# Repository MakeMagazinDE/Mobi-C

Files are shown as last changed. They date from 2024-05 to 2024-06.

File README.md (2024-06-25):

GitHub Logo

Maker Media GmbH

***

# Mobi-C

## Die mobile CNC-Fräse

**Dieser handliche X-Y-Positionierer für die Oberfräse ist schnell und einfach nachgebaut – dank fertig auf Länge bestellter Alu-Profile und Verbindungsteilen aus dem 3D-Drucker. Das ganze ist leicht zu transportieren, wird komplett mit Akkus betrieben und fräst auch in Werkstücke, die viel größer sind, als der Rahmen selbst.**

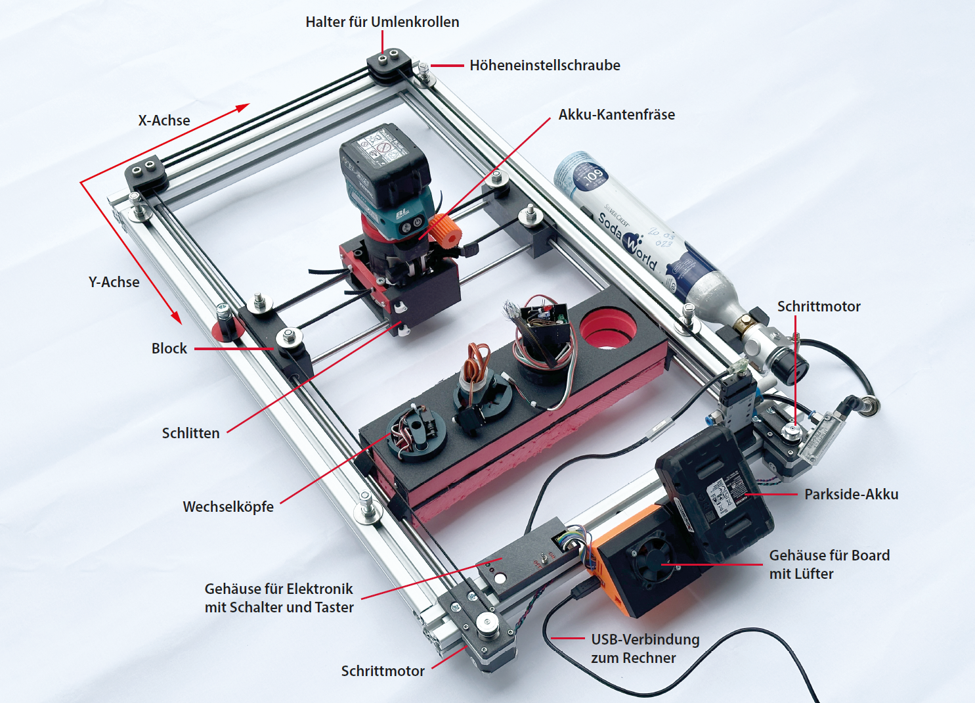
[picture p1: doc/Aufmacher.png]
Aufmacherbild aus dem Heft


Hier gibt es alles rund um den Nachbau der eigenen Mobi-C:

* Im Ordner _[cad](./cad/)_ liegt das 3D-Modell der Mobi-C als STEP-Datei und Projekt für Autodesk-Fusion 
* Im Ordner _[doc](./doc/)_ liegt unter anderem der [Schaltplan](./doc/schema.png)
* Im Ordner _[3d](./3d/)_ liegen die 3D-Druckvorlagen als STL-Dateien und gruppiert als 3mf, Details dazu weiter unten im Abschnitt **3D-Drucke**
* Im Ordner _[src](.src/)_ liegt das AutoHotkey-Skript fürs Einbauen der Pausen in den G-Code und im Zip-Archiv die EXE-Version davon

Der vollständige Artikel zum Projekt steht in der **[Make-Ausgabe 3/24 ab Seite 26](https://www.heise.de/select/make/2024/3/2401616284584453190)**. Einen ergänzenden Artikel mit weiteren Details zur Höhenverstellung, zur Frästiefen-Einstellung, zur Schleppmesser-Erweiterung und ein paar Erfahrungswerten gibt es **[online](https://heise.de/-9718002)**.

# Materialliste und Bezugsquellen
Vor einer Bestellung sind mit Hilfe der Tabelle im Heft und anhand der gewünschten Arbeitsbereichsgröße der eigenen Mobi-C die nötigen Profillängen **X** und **Y** sowie die Gleitstangenlängen **GX** und **GY** zu ermitteln.

* [2 Aluminiumprofile 40×40×**X** mm, Nut 8](https://www.dold-mechatronik.de/Aluminiumprofil-40x40L-I-Typ-Nut-8-leicht-176kg-m-Zuschnitt-50-6000mm)
* [2 Aluminiumprofile 40×40×**Y** mm, Nut 8, M8-Gewinde an den Stirnseiten anbringen lassen](https://www.dold-mechatronik.de/Aluminiumprofil-40x40L-I-Typ-Nut-8-leicht-176kg-m-Zuschnitt-50-6000mm)
* [2 Präzisionswellen 8×**GX**, geschliffen und gehärtet](https://www.dold-mechatronik.de/Praezisionswelle-8mm-h6-geschliffen-und-gehaertet-Material-CF53-mit-Bearbeitung)
* [2 Präzisionswellen 8×**GY**, geschliffen und gehärtet](https://www.dold-mechatronik.de/Praezisionswelle-8mm-h6-geschliffen-und-gehaertet-Material-CF53-mit-Bearbeitung)
* [Zahnriemen GT2, 6 mm, Länge laut Tabelle im Heft](https://www.dold-mechatronik.de/Zahnriemen-GT2-Breite-6mm-Meterware-Laenge-6-Meter)
* [5 Nutensteine mit Steg I-Typ 8 mit M8-Gewinde](https://www.dold-mechatronik.de/Nutenstein-mit-Steg-I-Typ-Nut-8-Gewindedurchmesser-M8)
* [7 Nutensteine mit Steg I-Typ 8 mit M6 Gewinde](https://www.dold-mechatronik.de/Nutenstein-mit-Steg-I-Typ-Nut-8-Gewindedurchmesser-M6)
* [4 Zylinderschrauben DIN 912 M8×40 (Innensechskant) für die Umlenkrollen am Rahmen](https://www.dold-mechatronik.de/DIN-912-Zylinderschraube-mit-Innensechskant-88-verzinkt-M8x40)
* [4 Zylinderschrauben DIN 912 M8×60 (Innensechskant) für die Umlenkrollen der X-Achse](https://www.dold-mechatronik.de/DIN-912-Zylinderschraube-mit-Innensechskant-88-verzinkt-M8x60)
* [4 DIN 7984 Zylinderschraube mit Innensechskant und niedrigem Kopf für die Rahmenmontage](https://www.dold-mechatronik.de/DIN-7984-Zylinderschraube-mit-Innensechskant-und-niedrigem-Kopf-88-verzinkt-M8x16)
* [4 Scheiben DIN9021 M8 - 8.4×32](https://www.dold-mechatronik.de/Scheibe-DIN9021-M8-84X32X2-A2)
* [4 Scheiben DIN125A-84 × M8](https://www.dold-mechatronik.de/Scheibe-DIN125A-M8x84-A2)
* [8 Kugellager 608ZZ (8×22×7)](https://www.dold-mechatronik.de/608ZZ-Bearings-8-x-22-x-7)
* [2 Z30-GT2-6 Riemenscheiben 5 mm Bohrung, 16 mm Sitz](https://www.bastelgarage.ch/z30-gt2-6-riemenscheibe-5mm-bohrung-16mm-sitz?search=z30-gt2)
* [8 Gleitlager LM8UU (8 mm Welle, 15×24 mm)](https://www.dold-mechatronik.de/Linearlager-8mm-LM8UU)
* 1 Meter Gewindestange M8 oder drei Schrauben M8, 100 mm lang mit Vollgewinde für die Höhenverstellung
* [4 Gewindeeinsätze M4](https://www.reichelt.com/ch/de/3d-druck-gewindeeinsaetze-m4x8-1-50-stueck-rx-m4x8-1-p332215.html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)
* 4 selbstsichernde Muttern M8
* 2 Stepper-Motoren (ST42sth38-1684A)
* [Arduino Uno USB](https://www.reichelt.com/ch/de/arduino-uno-rev-3-smd-variante-atmega328-usb-arduino-uno-p119045.html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)
* [CNC-Shield mit 4 Treibern A4988](https://www.reichelt.com/ch/de/arduino-shield-cnc-controllerboard-a4988-ard-shd-cnc-kit-p226375.html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)
* Lüfter 40×40×20 mm 12 bis 24 Volt
* 2 Schalter
* 1 Taster 
* 2 LEDs (eine rote, eine grüne)
* 2 Büroklammern
* [Parkside-Akku und Ladegerät](https://www.lidl.de/p/parkside-20-v-akku-2-ah-pap-20-b1-und-ladegeraet-2-4-a-plg-20-c1/p100368935)

# 3D-Drucke

 Als Material für alle 3D-Druck-Teile hat sich PLA bewährt, bei 0,2  Millimetern Schichtdicke. Als Infill reichen 15 %, außer bei den  Motorhaltern, die brauchen 80 %. Folgende Bilder zeigen, wie die Teile auf der Druckplatte angeordnet und orientiert werden sollten. Support ist nur an wenigen Stellen nötig: unter den Rundungen der Umlenkrollengehäuse  sowie beim Parkland-Akku-Adapter, auf den Screenshots.  

1. Hier alle Teile für den Rahmen, grün erkennt man den Support unter den Rundungen der Umlenkrollengehäuse:
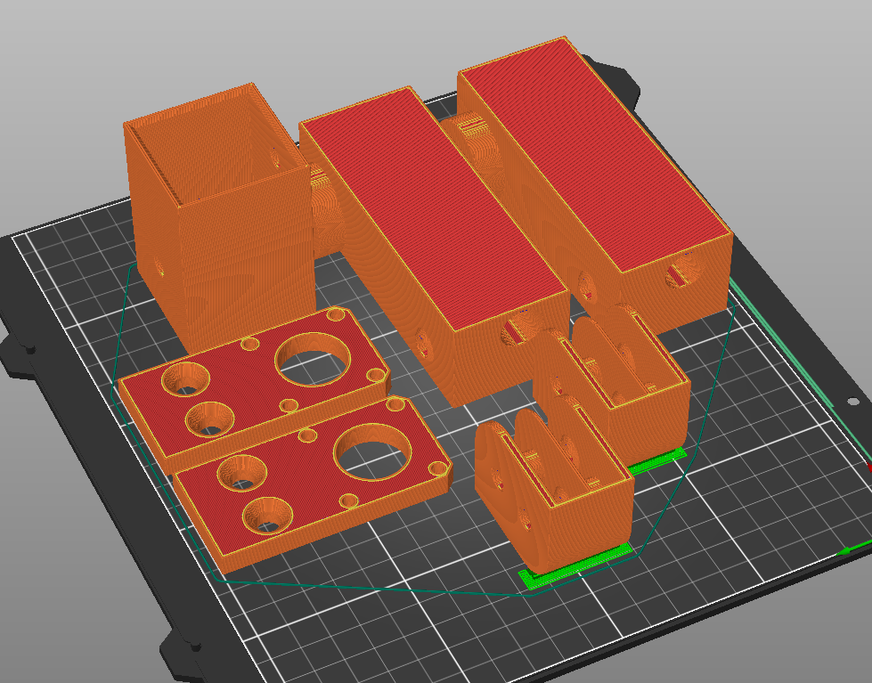
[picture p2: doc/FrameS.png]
Rahmen


2. Die Teile für den Schlitten werden nicht gestützt: 
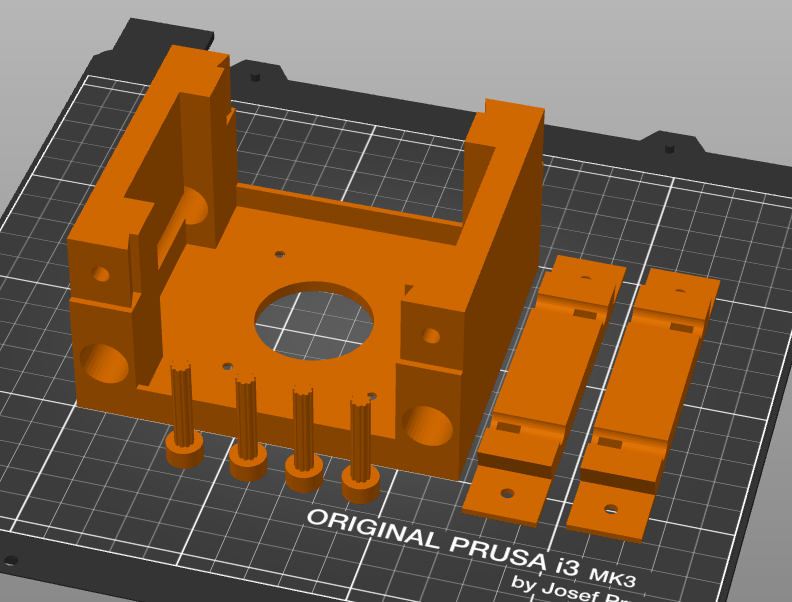
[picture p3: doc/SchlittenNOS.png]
Schlitten


3. Bei den Elektronikgehäusen muss der Adapter für den Parkside-Akku gestützt werden (vorne links):
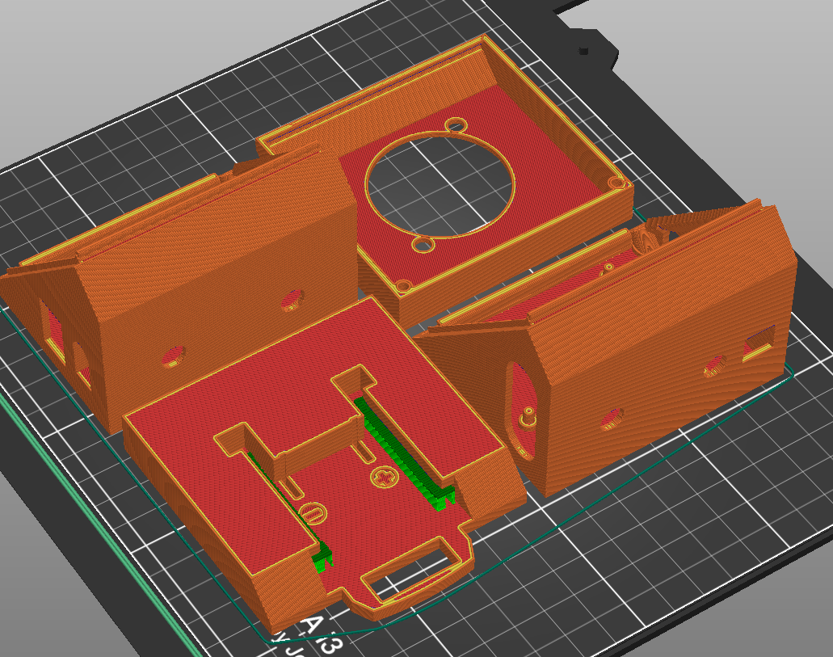
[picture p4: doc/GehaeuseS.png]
Elektronik


4. Das Schaltergehäuse braucht keine Stützen: 
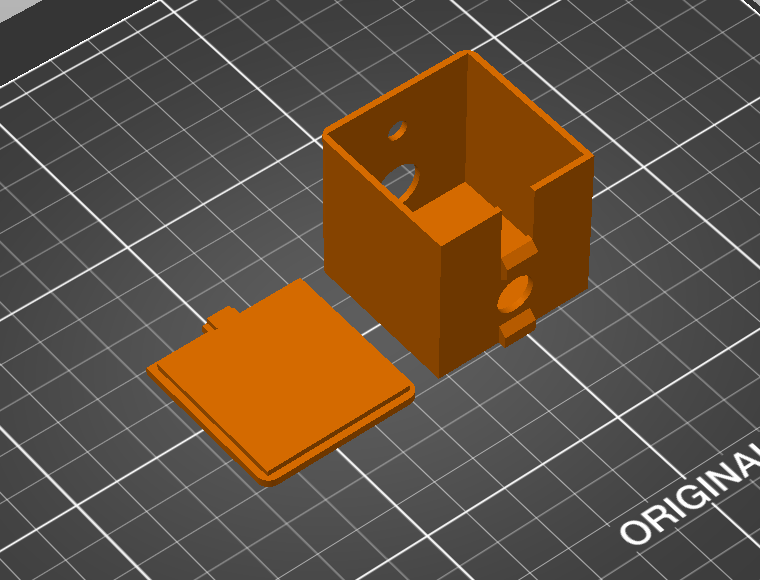
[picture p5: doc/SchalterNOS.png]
Schalter
   

5. Auch die Teile für die Makita müssen nicht gestützt werden:
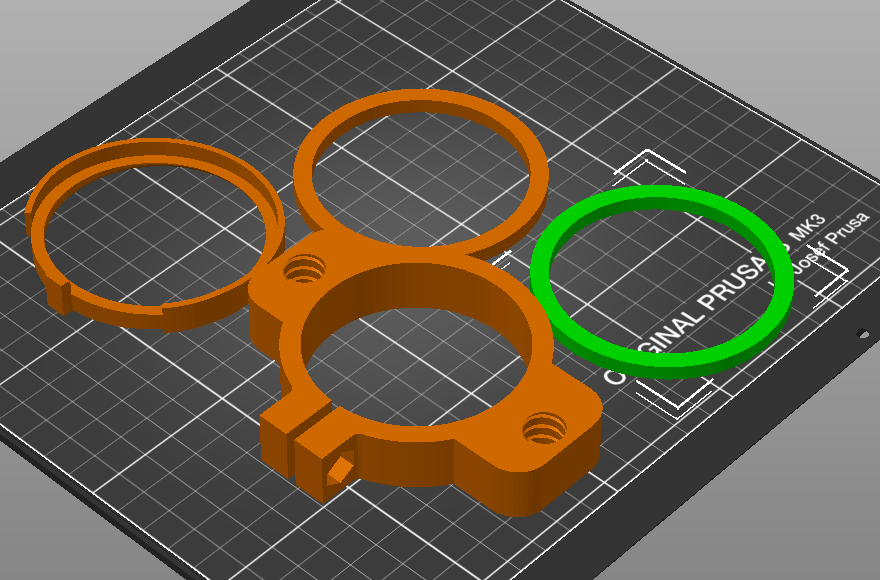
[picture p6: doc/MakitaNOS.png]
Makita
   

6. Die Ansicht für die Teile des Schleppmesseradapters sind hier der Deutlichkeit halber von schräg unten zu sehen: Grün bedeutet Support, die violette Fläche ist das erste Drucklayer:
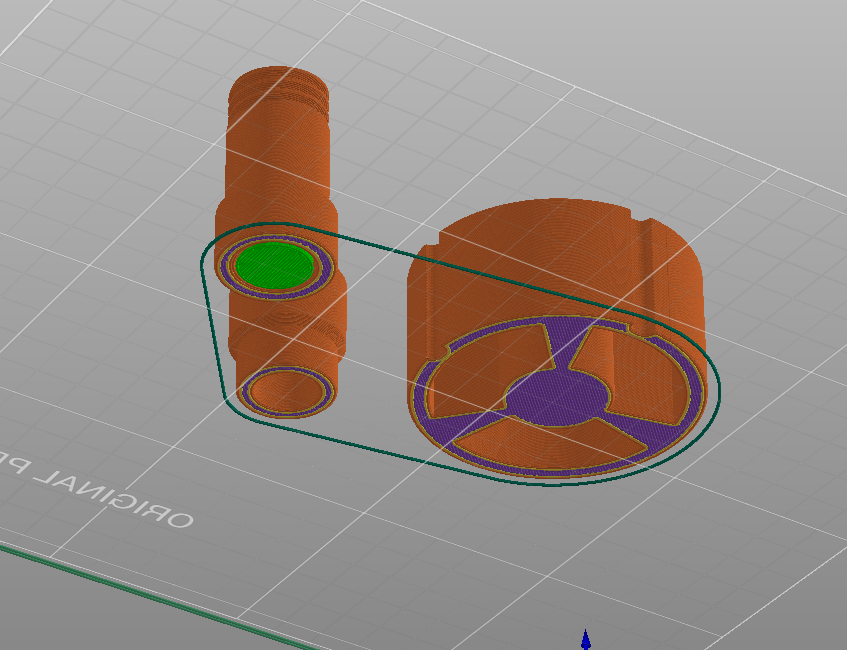
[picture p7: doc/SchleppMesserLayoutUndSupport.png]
Schleppmesser


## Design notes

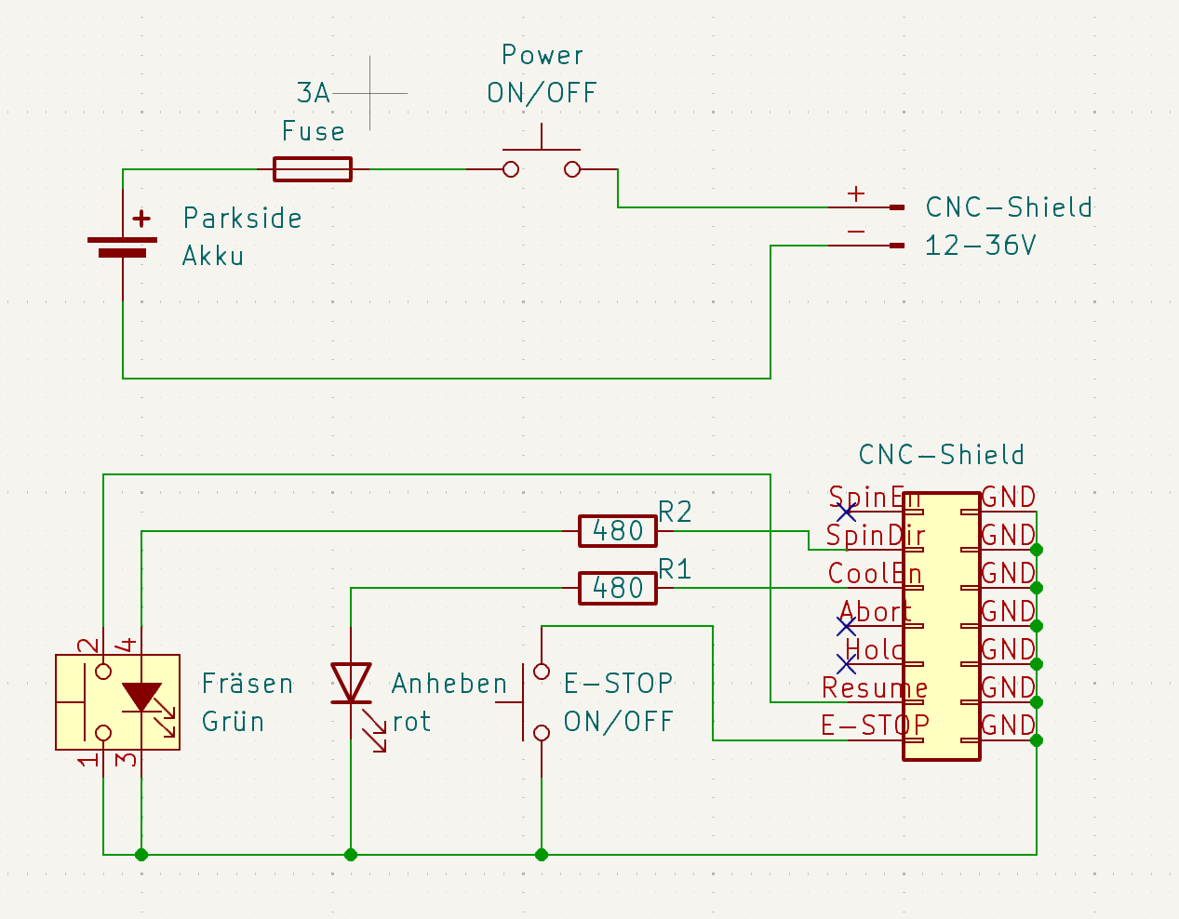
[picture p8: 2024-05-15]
doc/schema.png

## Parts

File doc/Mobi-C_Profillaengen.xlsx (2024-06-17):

Beschreibung | Anzahl | Länge [mm] | Max Länge [mm] | M8 Gewinde
Alu Profil 40x40 Richtung X-Achse | 2 | 470 | 480 | keine
Alu Profil 40x40 Richtung Y-Achse | 2 | 470 | 600 | beide Stirnseiten
Gleitstange X-Achse | 2 | 344 | 354
Gleitstange y-Achse | 2 | 510 | 640
Zahnriemen | 1 | 4260 | 4820
 | x-Richtung[mm] | y-Richtung[mm]
Arbeitsbereich | 216 | 352

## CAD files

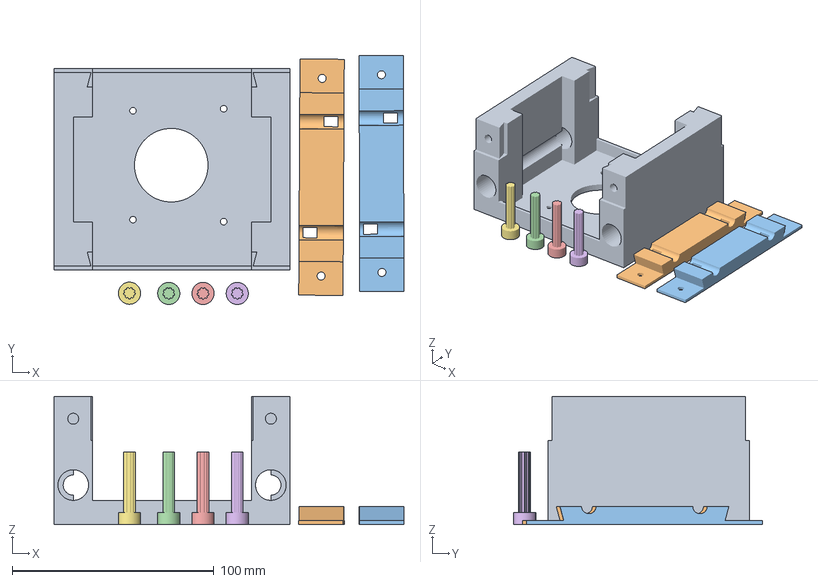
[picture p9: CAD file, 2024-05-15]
3d/Fraesschlitten/Fraesschlitten_complete_noSupports.3mf
173.6 x 123.5 x 63.6 mm
Fraesschlitten.stl
ZugRechtsLinks.stl
RiemenSpanner.stl

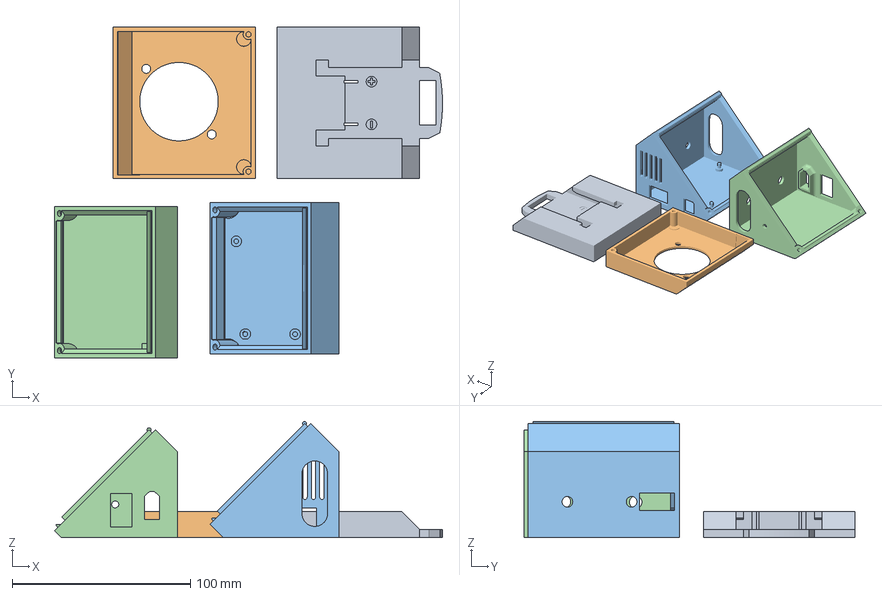
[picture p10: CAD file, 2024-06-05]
3d/ElectronikGehaeuse/ElectronicHousingComplete_Bambu.3mf
217.7 x 185.4 x 65.1 mm
lidl_parkside_20v_battery_adapter_front_85mm.stl
ElectronicHousing_front.stl
ElectronicHousing_rear.stl
lidl_parkside_20v_battery_adapter_rear_85mm.stl

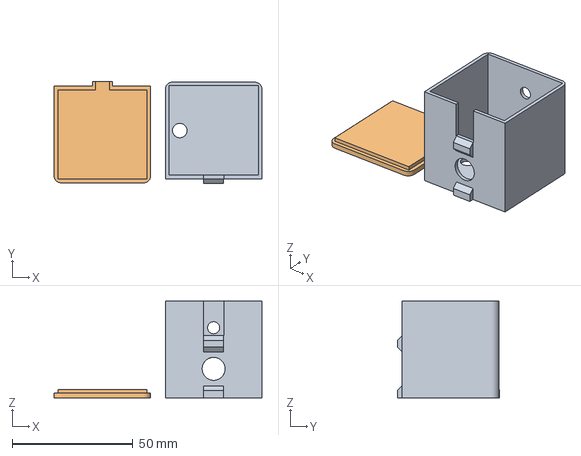
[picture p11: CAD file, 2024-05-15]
3d/ElectronikGehaeuse/SwitchLED_Housing_Complete.3mf
86.0 x 42.3 x 40.0 mm
SwitchCore.stl
SwitchCover.stl

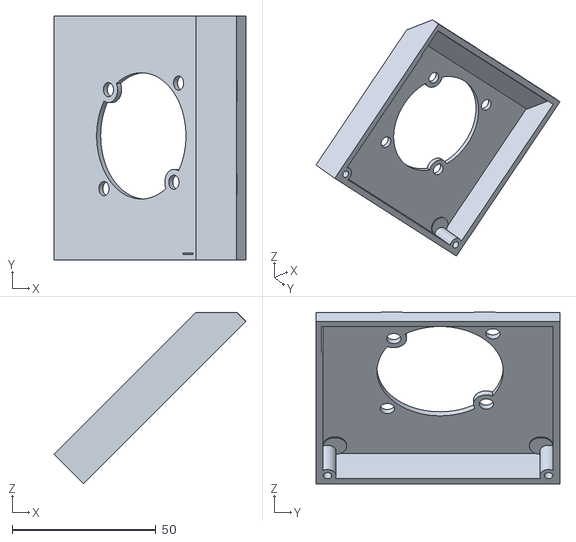
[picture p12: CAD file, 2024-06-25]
3d/ElectronikGehaeuse/ElectronicHousing_front.stl
66.9 x 85.0 x 59.8

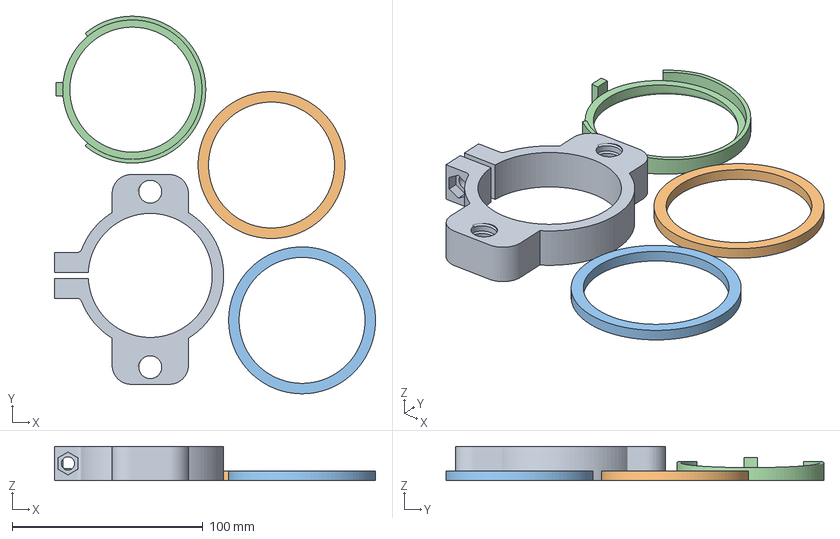
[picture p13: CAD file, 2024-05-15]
3d/MakitaZubehoer/MakitaZubehör_NoSupport.3mf
168.3 x 197.9 x 18.0 mm
StopBracket.stl
Distanzring_5mm.stl
FraesSchuh_Begradigung.stl

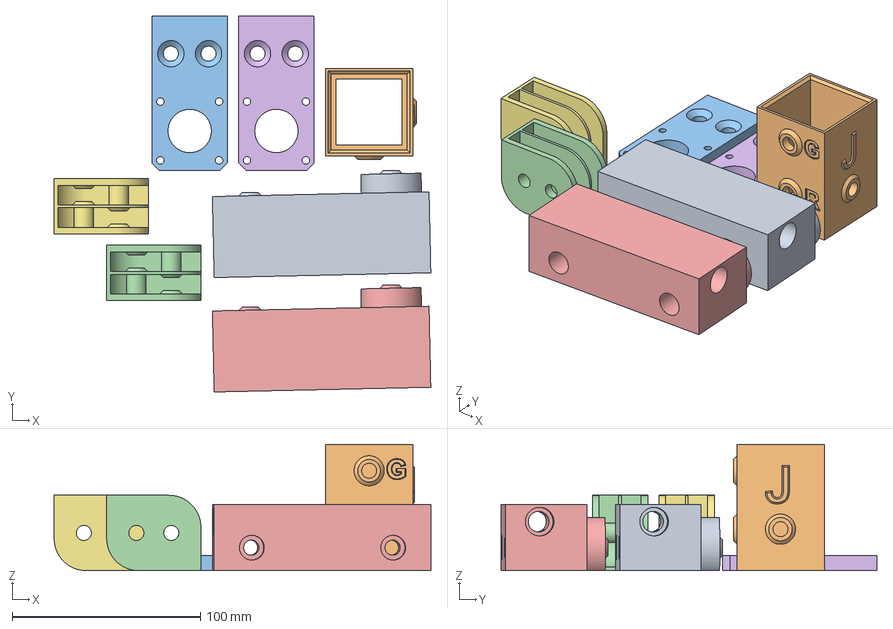
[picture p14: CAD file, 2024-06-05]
3d/Rahmen/Rahmen_LayoutAndSupport_Bambu0p6.3mf
199.9 x 199.5 x 67.0 mm
BlockXachse.stl x 2
BohrSchablone.stl
Motorhalter.stl x 2
UmlenkrollenGehaeuse.stl x 2

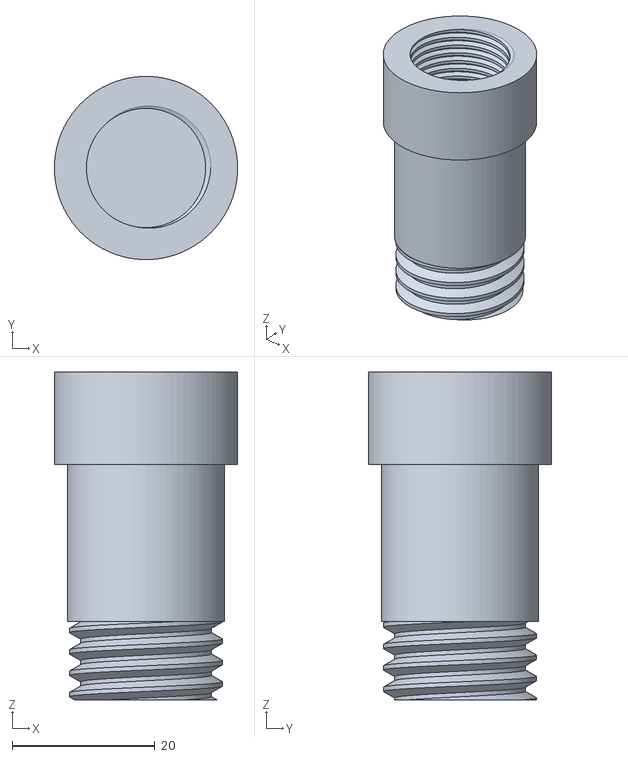
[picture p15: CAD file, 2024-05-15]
3d/Schleppmesser/HalterCore.stl
25.7 x 25.7 x 46.0

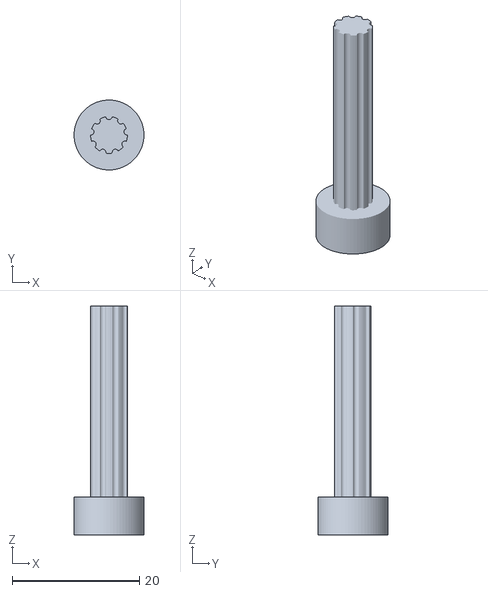
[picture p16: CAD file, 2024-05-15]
3d/Fraesschlitten/RiemenSpanner.stl
11.0 x 11.0 x 36.0

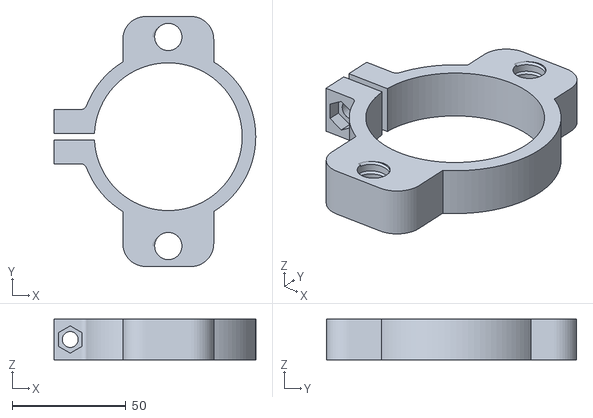
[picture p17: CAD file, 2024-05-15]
3d/MakitaZubehoer/StopBracket.stl
88.7 x 110.0 x 18.0

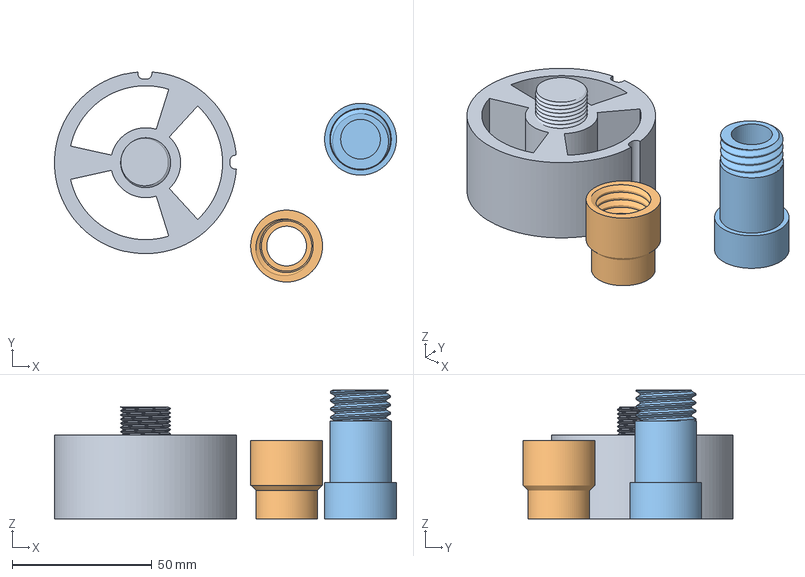
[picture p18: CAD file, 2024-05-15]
3d/Schleppmesser/SchleppMesserAdapter.3mf
122.3 x 75.1 x 46.0 mm
SchleppMesserAdapter.stl
HalterKappe.stl
HalterCore.stl

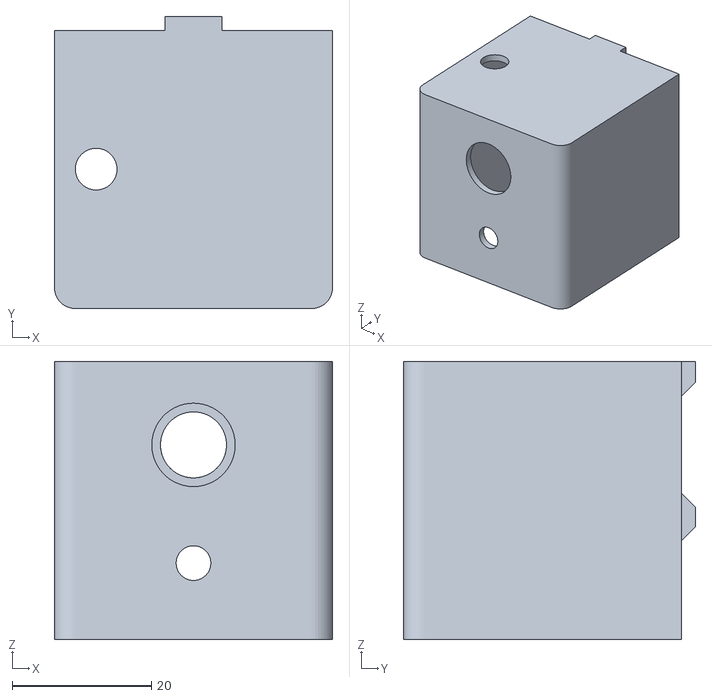
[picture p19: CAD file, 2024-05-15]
3d/ElectronikGehaeuse/SwitchCore.stl
40.0 x 42.0 x 40.0

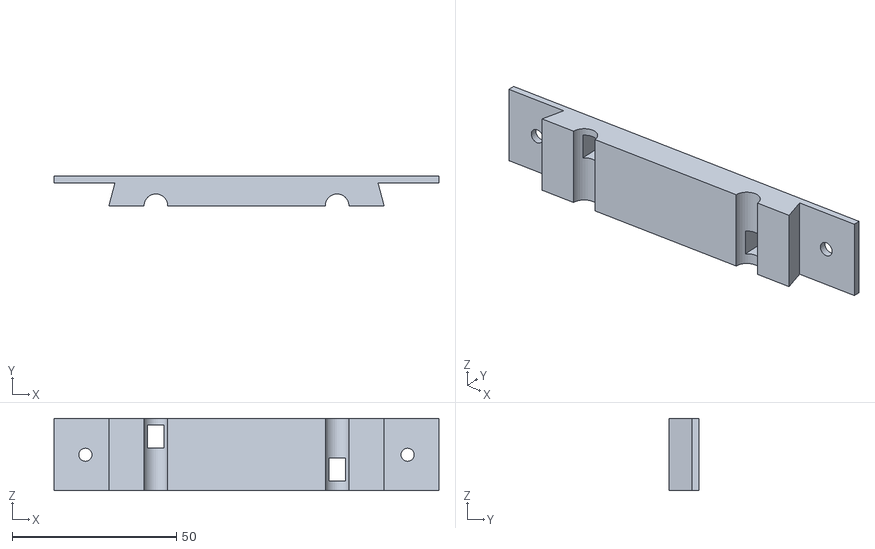
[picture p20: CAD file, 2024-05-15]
3d/Fraesschlitten/ZugRechtsLinks.stl
117.1 x 9.00 x 22.0

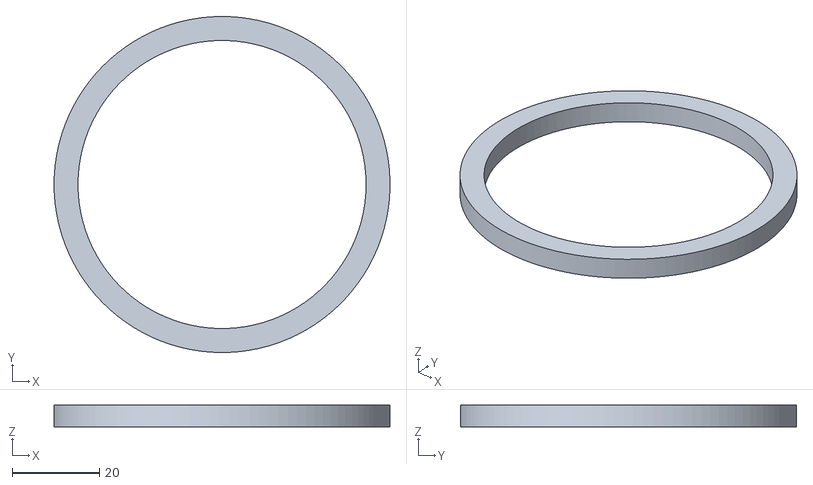
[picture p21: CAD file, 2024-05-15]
3d/MakitaZubehoer/Distanzring_5mm.stl
77.0 x 77.0 x 5.00

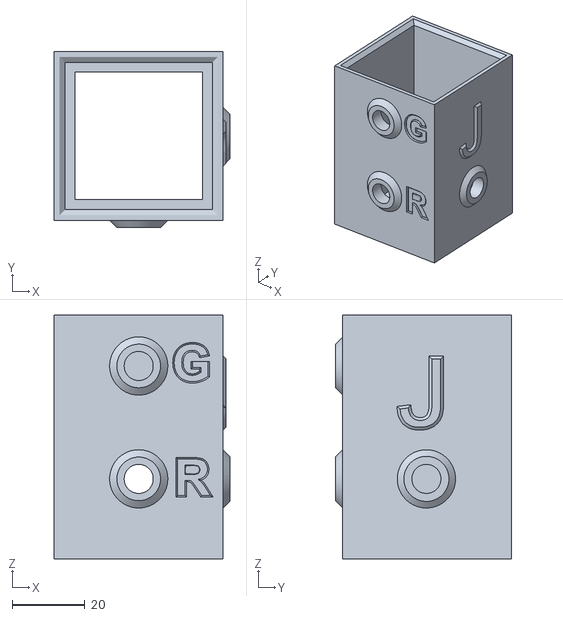
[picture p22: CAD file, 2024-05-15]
3d/Rahmen/BohrSchablone.stl
48.2 x 48.4 x 67.0

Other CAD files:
3d/Rahmen/Rahmen_LayoutAndSupport.3mf
3d/Schleppmesser/HalterKappe.stl
3d/ElectronikGehaeuse/SwitchCover.stl
3d/Fraesschlitten/Fraesschlitten.stl
3d/ElectronikGehaeuse/ElectronicHousing_rear.stl
3d/ElectronikGehaeuse/lidl_parkside_20v_battery_adapter_front_85mm.stl
3d/ElectronikGehaeuse/lidl_parkside_20v_battery_adapter_rear_85mm.stl
3d/MakitaZubehoer/FraesSchuh_Begradigung.stl
3d/Rahmen/BlockXachse.stl
3d/Rahmen/Motorhalter.stl
3d/Rahmen/UmlenkrollenGehaeuse.stl
3d/Schleppmesser/SchleppMesserAdapter.stl

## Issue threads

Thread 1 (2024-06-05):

Wenn schon Parkside dann richtig - Verwendung von POFA 12 B3

Knochi, 2024-06-05:
Hi,

ich hab heute das Projekt gesehen und direkt an meine Akku-Kantenfräse von Parksite gedacht. Dann habe ich auch noch gelesen, dass ein Parkside Akku zum Antrieb der Motoren genutzt wird.

Wäre es nicht naheliegend auch noch einen Adapter für die [Parkside Kantenfräse](https://www.lidl.de/p/parkside-12-v-akku-oberfraese-pofa-12-b3-ohne-akku-und-ladegeraet/p100347300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) zu entwickeln?

JonahPi, 2024-06-17:
Der Akku für die Parkside Kantenfräse entspricht nicht dem Akku, der für den Antrieb verwendet wird. Die Makita ist sehr handlich und der Frässchuh lässt die einfache Entwicklung von weiteren Adaptern zu. Das CAD File steht jedoch als Source-File zur Verfügung.

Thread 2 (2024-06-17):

Materialliste: M8-Gewinde an der falschen Achse

ambranaam, 2024-06-17:
In der Materialliste heisst es:
[*2 Aluminiumprofile 40×40×X mm, Nut 8, M8-Gewinde an den Stirnseiten anbringen lassen*]

Im Artikel steht aber der Kommentar "M8-Gewinde auf beiden Stirnseiten" bei den Y-Achsen-Aluprofilen und auch vom Aufbau her machen die Gewinde auf der Y-Achse mehr Sinn.

JonahPi, 2024-06-17:
Das X bezieht sich nur auf den Wert, den man der Tabelle entnehmen muss. Es ist richtig, dass nur die Profile in y-Richtung Gewinde in der Stirnseite benötigen.

ambranaam, 2024-06-17:
Wird dann die Materialliste noch geändert?

Da heisst es ja jetzt noch:
[2 Aluminiumprofile 40×40×X mm, Nut 8, M8-Gewinde an den Stirnseiten anbringen lassen*]
[2 Aluminiumprofile 40×40×Y mm, Nut 8]

Das müsste meiner Meinung nach geändert werden zu:
[2 Aluminiumprofile 40×40×X mm, Nut 8]
[2 Aluminiumprofile 40×40×Y mm, Nut 8, M8-Gewinde an den Stirnseiten anbringen lassen]

JonahPi, 2024-06-17:
Ich habe ein entsprechendes Excel-File im Folder doc abgelegt, dort sollte es stimmen

ambranaam, 2024-06-18:
Danke, aber ich hatte eher an die Materialliste im _README.md_ gedacht. Das ist ja der Text, den man zuerst sieht, wenn man das Projekt im Browser öffnet, und da sind ja auch Links hinterlegt, also werden einige (so wie ich) das direkt von da so nutzen wollen.

ambranaam, 2024-06-25:
Danke für die Änderung, so passt's jetzt.

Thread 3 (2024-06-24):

Materialliste: falscher Lüfter

ambranaam, 2024-06-24:
In der Materialliste im _**README.md**_ ist ein falscher Lüfter eingetragen.
Ein 40x40x20-Lüfter passt da nicht, die Löcher im Gehäusedeckel sind für einen 45x45-Lüfter, und falls man den auf der Innenseite des Deckels anbringen möchte, sollte die Dicke auch nicht 20mm betragen, sondern eher 10mm.

Leider scheint es nur sehr wenige 45x45-Lüfter mit 24V zu geben. Könnte man da das 3D-Modell abändern und ein 50x50-er Loch draus machen? Dann hat man eine viel größere Auswahl an Lüftern.

Vielleicht wird das aber auch mein erster Einsatz der Fräse: das bestehende 45x45-Loch zu einem 50x50-Loch auszufräsen.

JonahPi, 2024-06-25:
Vielen Dank für den Hinweis, hier ist leider ein Fehler unterlaufen. Das STL-File ist nun so angepasst, dass sowohl 40mm als auch 45mm Lüfter montiert werden können. Für grössere Lüfter einfach zusätzliche Löcher bohren.

ambranaam, 2024-06-25:
Danke, so kann ich meinen 40x40-Lüfter doch noch verwenden.

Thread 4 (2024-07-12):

Datei fehlt

ambranaam, 2024-07-12:
Hi,

irgendwie vermisse ich die im Artikel versprochene Datei **FlightTest.nc**.
Wird die noch hinzugefügt? Oder kann man die woanders finden?

JonahPi, 2024-08-09:
I added the flight-test file to the src folder.

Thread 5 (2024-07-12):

GCode-Converter in Python

ambranaam, 2024-07-12:
Ich habe mal den GCode-Converter von Autohotkey nach Python übersetzt.
Damit kann man dann einfach per `Rechts-Click` - `Senden an` die Konvertierung vornehmen.

Zu finden hier:
https://github.com/ambranaam/13af7880-3708-4ab4-ac3e-06d1ec23ab0c

ambranaam, 2024-07-12:
Ach ja - getestet hab ich das bisher nur "theoretisch", das erzeugte File sieht soweit plausibel aus.
"Live" an der Mobi-C hab ich's noch nicht ausprobiert.

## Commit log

2024-06-05 Electronic Housing Collection updated
    The back of the electronic housing has been updated with a version, which allows more space for the PCB
    [ElectronicHousingComplete.3mf, ElectronicHousingComplete_Bambu.3mf, Rahmen_LayoutAndSupport_Bambu0p6.3mf]
2024-06-17 Excel table to calculate correct profile length
    [Mobi-C_Profillaengen.xlsx]
2024-06-25 Gehäuse für 40 und 45mm Lüfter
    [ElectronicHousing_front.stl]
2024-06-25 Update README.md
    M8 Gewinde and Stirnseiten der Y-Profile hinzugefügt, Gewinde an Stirnseiten der X-Profile entfernt
2024-08-09 Sample File for Mobi-C milling
    Engraving a 20x20mm square starting from position X = 10, Y = 10
